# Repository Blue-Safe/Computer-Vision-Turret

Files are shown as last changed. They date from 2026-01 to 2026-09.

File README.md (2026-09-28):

# Computer Vision Turret (CVT)

CVT is a real-time computer vision turret designed to track a moving black target from ~5 ft away and maintain alignment within one-fourth of the target’s area.  
The system combines proportional and predictive control and is split across a Raspberry Pi 5 (vision and logic) and a Raspberry Pi Pico (servo and laser control).

> This project was designed, built, tested, and documented independently.

## Skills Demonstrated

- Embedded systems architecture with delegated responsibility
- Computer vision with OpenCV
- Real time control concepts
- UART communication
- Data logging and statistical analysis
- Test design and performance evaluation
- Iterative debugging across software and hardware

### Mechanical Design

- Custom turret frame modeled in Fusion 360
- 3D printed structural and mounting componets
- Design iteration focused on rigidity, airflow, and quick iterations 

## System Architecture

### Raspberry Pi 5 (High-Level Control)
- Captures live video feed from webcam
- Performs computer vision using OpenCV
- Determines system state and target behavior
- Estimates target velocity and predicts future position
- Sends motion commands to the Pico over UART

### Raspberry Pi Pico (Real-Time Control)
- Receives commands from the Pi
- Converts desired angles into PWM signals
- Drives X/Y servos and toggles the laser

## Videos and Pictures

**Demo**  
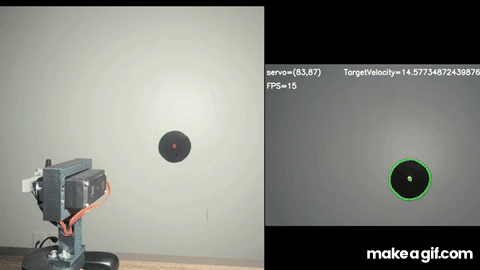
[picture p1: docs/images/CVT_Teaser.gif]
CVT Teaser


**Full Test Footage**
- Static target test: [Here](https://youtu.be/bPHvd_qhFpg)
- Dynamic target test: [Here](https://youtu.be/34uFZd7rjXk)

### Build Photos

| Front | Side |
|---|---|
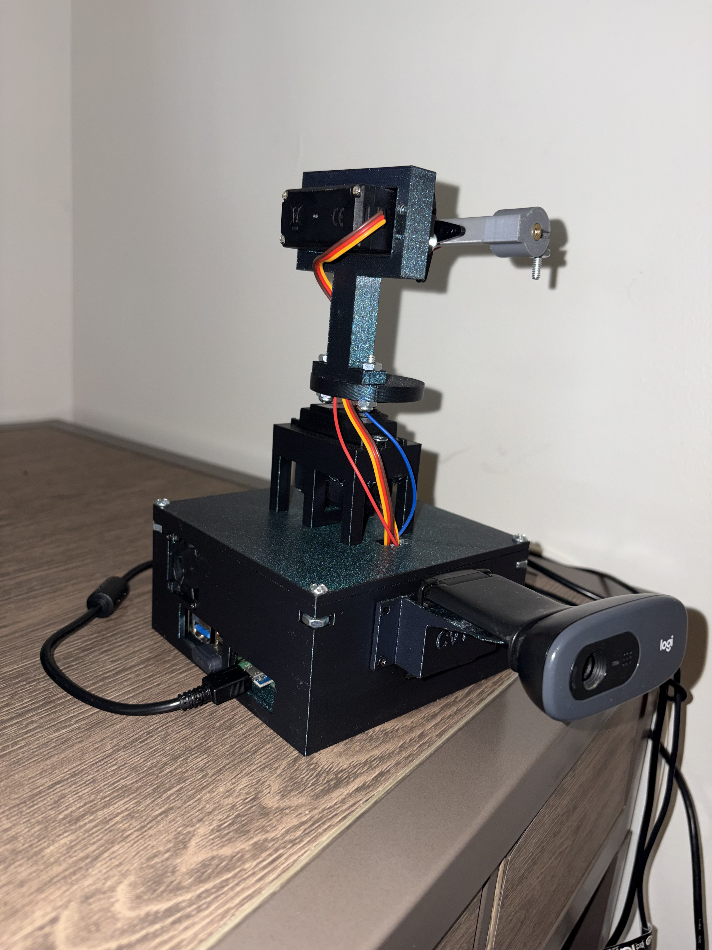
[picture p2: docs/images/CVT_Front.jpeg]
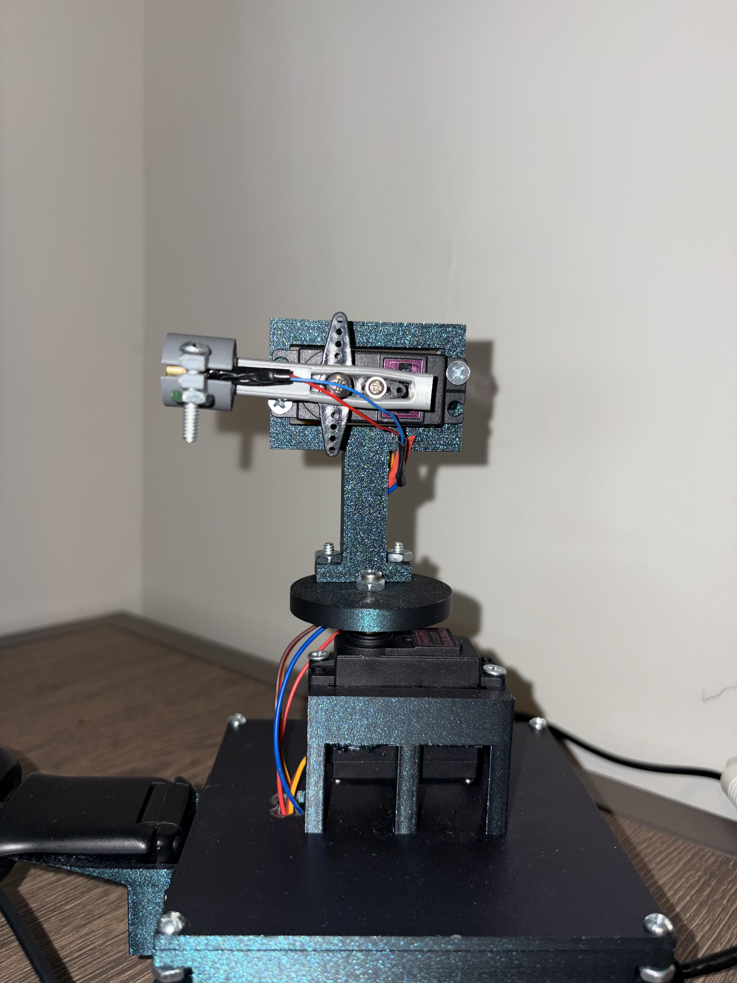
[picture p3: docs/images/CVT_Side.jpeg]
|  |  |

| Inside | Rear |
|---|---|
|  |  |

## What It Does

- Detects a target in a live camera feed 
- Determines target position and laser position, then calculates pixel error
- Stores information of target and the turrets current state
- Applies proportional and predictive movement, deadbanding, and motion constraints
- Converts pixel error into servo motion commands
- Maintains tracking under target motion and noise
- Logs runtime data to CSV for performance analysis

## Control Loop Overview

1. Capture frame  
2. Threshold and filter to isolate target then laser  
3. Extract contours and select best candidate based on expected area and color  
4. Compute target center and pixel error  
5. Apply control logic (proportional and predictive)  
6. Send servo commands over UART  
7. Log timestamped data (position, error, velocity, state)

## Results and Performance

### Tracking Error vs Target Velocity
This plot compares tracking error against target velocity over time, highlighting the velocity range where the system performs reliably and where hardware limits (camera FPS) introduce error. You can see tracking error increase once target velocity exceeds ~125 px/s, which correlates with the system's frame rate and control update limits.

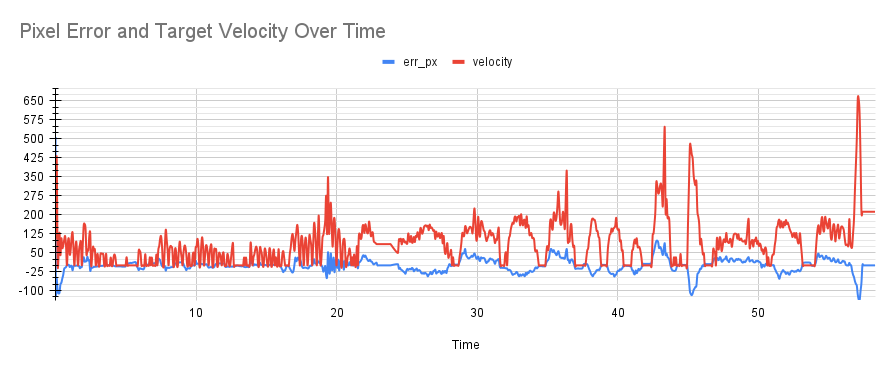
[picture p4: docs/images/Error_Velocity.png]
Error vs Velocity


### Lock-In Time Histogram
Distribution of Lock-In times. Locked In was defined as remaining within one-fourth the area of the target for half a second. CVT averaged a lock in time of .98 seconds, with a standard deviation of .27 seconds. By the Lock-In definition, acquisition time is around .48 seconds.

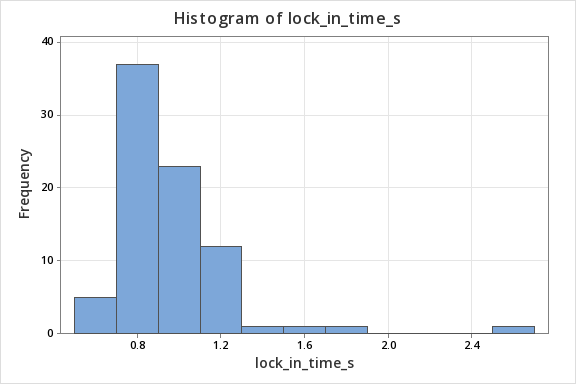
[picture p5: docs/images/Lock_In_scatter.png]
Lock-In Histogram


### Limitations and Constraints

- Camera operates at ~15 FPS, limiting control update rate
- Higher target velocities (>125 px/s) increase tracking error
- Lighting conditions affect thresholding reliability

These constraints were intentionally measured and documented to define realistic system performance bounds. See [this log](data/sample/DYNAMIC_TARGET.csv) for documented framerate.

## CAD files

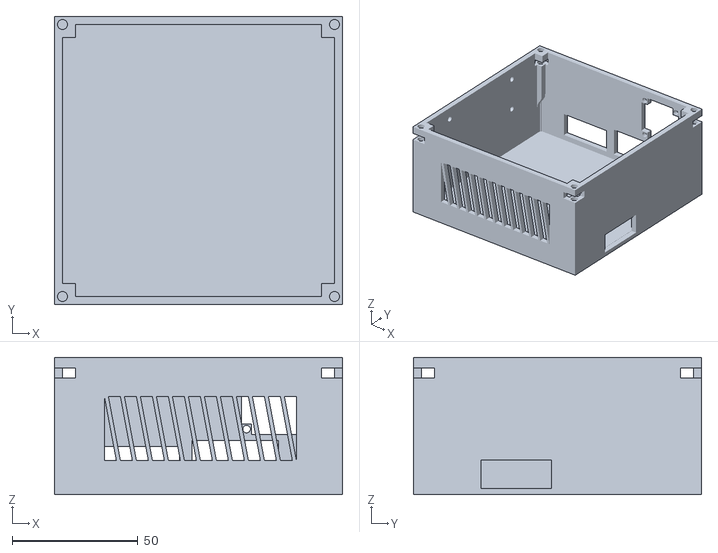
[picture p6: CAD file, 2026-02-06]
stl/CVT_Base.stl
114.3 x 114.3 x 54.5

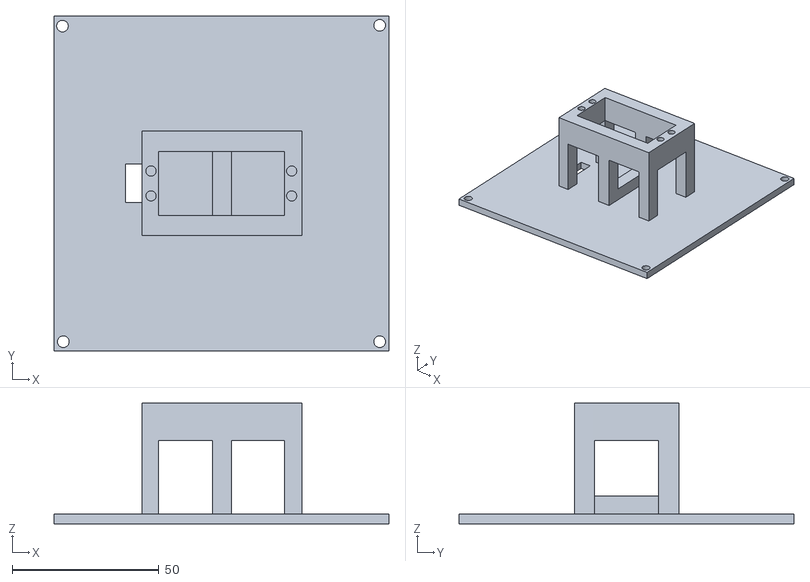
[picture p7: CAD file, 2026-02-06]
stl/CVT_Lid.stl
114.3 x 114.3 x 41.2

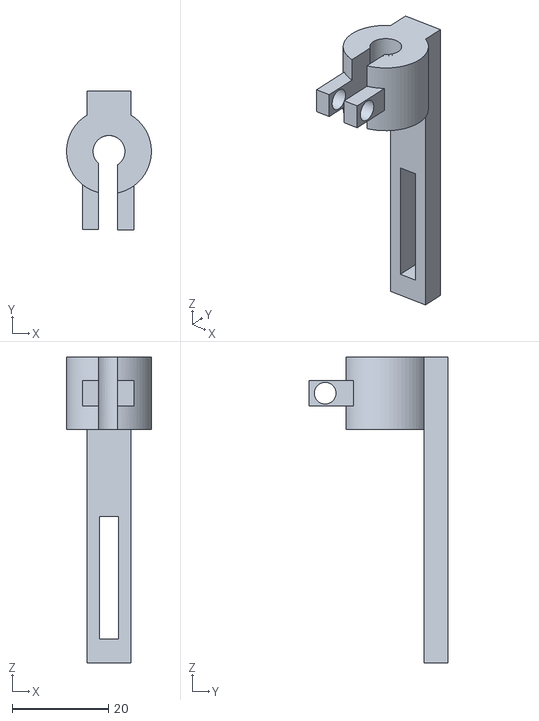
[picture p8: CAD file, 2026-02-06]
stl/CVT_LaserMount.stl
17.6 x 28.8 x 63.5

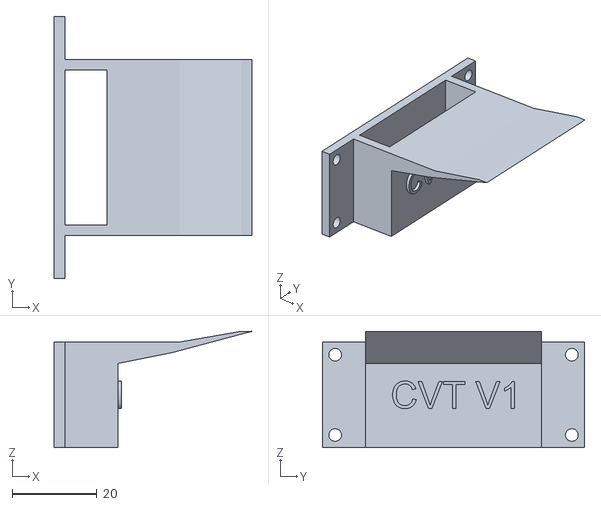
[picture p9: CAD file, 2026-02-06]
stl/CVT_CameraMount.stl
46.8 x 62.0 x 27.5

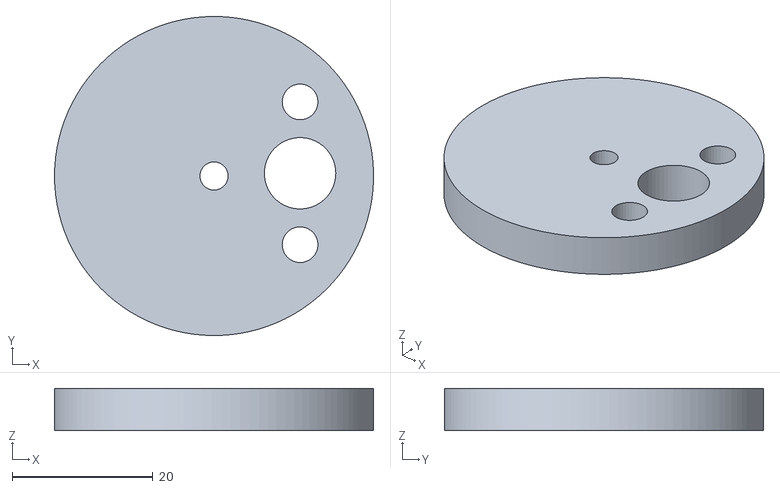
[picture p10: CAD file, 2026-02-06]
stl/CVT_AxisAdapter.stl
45.4 x 45.4 x 6.00

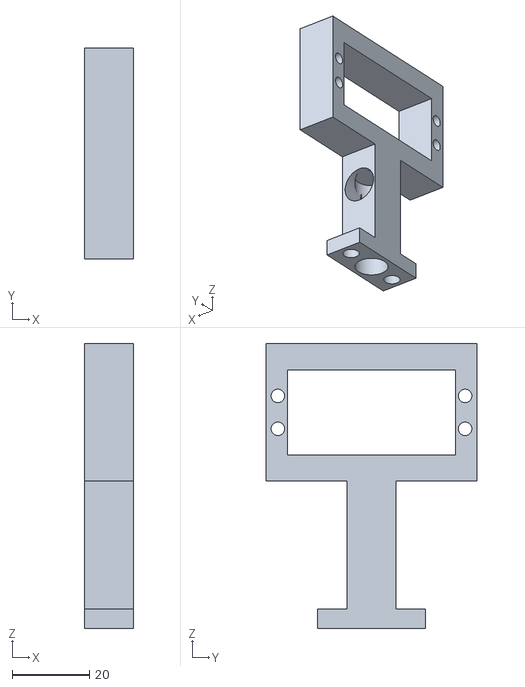
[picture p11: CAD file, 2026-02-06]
stl/CVT_ServoMount.stl
12.7 x 54.6 x 73.7

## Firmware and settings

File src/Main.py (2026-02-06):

import cv2
import numpy as np
import time
import math
import csv
from pathlib import Path
from enum import Enum, auto
from dataclasses import dataclass
from Servo_Control import sendData

# Tunable Variables 
DEADBAND_PX = 7
LASER_AREA  = 5000
TARGET_AREA = 8000
LOCKED_PX = math.sqrt(TARGET_AREA / math.pi) / 2
MAX_ANGLE = 170
MIN_ANGLE = 10
MAX_ANGLE_JUMP = 30
LOST_COUNT = 15
PTD_CONSTANT = 0
VEL_THRESHOLD = 30
T_LEAD = .22
LOCKED_TIME =.5
CONFIDENCE_THRESHOLD = 80
TAU = 0.7
WIDTH = 640
HEIGHT = 480
DIVISIONS = 10

# Invert if turret tracks in the wrong direction
INVERT_X = True
INVERT_Y = False

# Turn on/off debugging tools
Debug = False
UI = True
frameRate = True
AllMasks = False

# Establish States

class State(Enum):
    TRACK = auto()
    IDLE = auto()
    INIT = auto()
    TESTONE = auto()
    TESTTWO = auto()


# Define Turret object. This organizes the variables I edit in many
# spots, without having the headache of globals

@dataclass
class Turret:
    state: State = State.INIT
    servo_x: float = 90.0
    servo_y: float = 90.0
    home_pos: tuple[int,int] = (0,0)
    target_pos: tuple[int,int] = (0,0)
    last_target: tuple[int,int] = (0,0)
    laser_pos: tuple[int,int] = (0,0)

    lost_counter: int = 0
    locked: bool = False
    lock_start: float = 0.0
    lock_in_time: float = 0.0
    t_lock: float = 0.0
    confidence: float = 0.0
    accuracy: float = 0.0

class CSVLogger:

    def __init__(self):
        self.f = None
        self.w = None
        self.t0 = None

    def start(self, filename: str):
        Path("logs").mkdir(exist_ok=True)
        self.f = open(Path("logs") / filename, "w", newline="")
        self.w = csv.writer(self.f)
        self.t0 = time.perf_counter()

        self.w.writerow([
            "t", "dt", "fps", "state",
            "laser_x", "laser_y",
            "target_x", "target_y",
            "dx", "dy", "err_px",
            "vx", "vy", "velocity",
            "servo_x", "servo_y",
            "locked", "t_lock",
            "lost_counter"
        ])



    def log_frame(self, t: Turret, dt, dx, dy, err_px, vx=0,vy=0):
        if self.w is None:
            return

        rel_t = time.perf_counter() - self.t0

        self.w.writerow([
            round(rel_t, 4), round(dt, 4), round(1.0/dt), t.state.name,
            int(t.laser_pos[0]), round(1.0/dt), int(t.laser_pos[1]),
            int(t.target_pos[0]), int(t.target_pos[1]),
            round(dx, 3), round(dy, 3),
            round(vx,3), round(vy,3),round(math.hypot(vx+.00001,vy+.00001)),
            round(err_px, 3),round(t.servo_x, 3), round(t.servo_y, 3),
            int(t.locked), round(t.t_lock, 4)
        ])

    def stop(self):
        if self.f:
            self.f.close()
        self.f = None
        self.w = None
        self.t0 = None

    @property
    def enabled(self):
        return self.w is not None

class Dummytarget:

    pos: tuple[int,int] = (0,0)
    velocity: tuple[float,float] = (0.0,0.0)
    area: float = TARGET_AREA 

    def __init__(self,pos,velocity):
        self.pos = pos
        self.velocity = velocity

    def move(self,dt):
        # Determine next position based off of the current velocity and time passed.

        x,y = self.pos
        dx,dy = self.velocity[0]*dt,self.velocity[1]*dt
        self.pos = x+dx,y+dy

def save_trials_csv(time_trials: dict, filename: str):
    Path("logs").mkdir(exist_ok=True)
    with open(Path("logs")/filename, "w", newline="") as f:
        w = csv.writer(f)
        w.writerow(["trial_id","goal_x","goal_y","lock_in_time_s"])
        for i, ((x,y), tlock) in enumerate(time_trials.items()):
            w.writerow([i, x, y, tlock])


def largest_center_from_mask(mask, min_area,max_area):
    # Helper function that finds all contours within the frame, then orgainzes them
    # and returns the position and contour object that is the largest within the range 
    # Passed through the parameters

    contours, _ = cv2.findContours(mask, cv2.RETR_EXTERNAL, cv2.CHAIN_APPROX_SIMPLE)
    valid = []
    for c in contours:
        if cv2.contourArea(c) >= min_area and cv2.contourArea(c) <= max_area:
            valid.append(c)
    
    if not valid:
        return None, None
    
    c = max(valid, key=cv2.contourArea)
    x, y, w, h = cv2.boundingRect(c)
    cx, cy = x + w // 2, y + h // 2
    if Debug:
        print(f"Biggest Blob size: {cv2.contourArea(c)}")
    return (cx, cy), c

def detect_laser(frame_bgr):
    hsv = cv2.cvtColor(frame_bgr, cv2.COLOR_BGR2HSV)

    # Laser appears bright red and white hot to the webcam. I use three ranges, as red wraps around the scale and
    # If we don't account for the white center, it'll be a donut shape rather than our whole laser.
    RL1, RU1 = (0, 60, 120), (10, 255, 255)
    RL2, RU2 = (170, 60, 120), (179, 255, 255)
    WL, WU = (0, 0, 200), (179, 10, 255)

    m1 = cv2.inRange(hsv, RL1, RU1)
    m2 = cv2.inRange(hsv, RL2, RU2)
    m3 = cv2.inRange(hsv, WL, WU)


    # To get each pixal we picked out, we have to or all our maskes together. We have to embedded the call
    # Inside because it only takes two arguments
    mask = cv2.bitwise_or(cv2.bitwise_or(m1, m2), m3)

    # Help clean specks
    mask = cv2.medianBlur(mask, 5)

    # Pass off to our helper to get the largest blobs center.
    # Range is geneours because the webcame is noisy.
    center, contour = largest_center_from_mask(mask, LASER_AREA-5000,LASER_AREA+5000)

    # Return the center cord, the masked frame incase we want to display it, and the actual object itself. 
    return center, mask, contour

def detect_target(frame_bgr, laser_mask=None):

    # The goal of this helper is to find the largest object in the frame while not picking up the laser.
    # Thats why we pass laser_maks through, so we automatically block out where it is from the target mask.
    
    # Convert color range to hsv for color tracking

    hsv = cv2.cvtColor(frame_bgr, cv2.COLOR_BGR2HSV)

    # Filter for colors within the expected color range of the target.

    BL,BU = (0,0,0),(179,255,50)


    mask = cv2.inRange(hsv,BL,BU)

    

    # This is where we block out where the laser is in the frame, or atleast where it was when we last located it.
    if laser_mask is not None:
        inv_laser = cv2.bitwise_not(laser_mask)
        mask = cv2.bitwise_and(mask, inv_laser)

    # Pass off largest blob detection to helper function.

    center, contour = largest_center_from_mask(mask, TARGET_AREA-3000, TARGET_AREA+3000)
    
    return center, mask, contour

def clamp(val, low, high):
    return max(low, min(high, val))

def move_servos(t:Turret,dx,dy,gain):
    # Moves the servos based on their current position, the error, and gain.

    # If Servo moves in the wrong direction flip axis's
    if INVERT_X:
        dx = -dx
    if INVERT_Y:
        dy = -dy

    # pixels to degrees
    X_degree = (dx / PTD_CONSTANT) * gain
    Y_degree = (dy / PTD_CONSTANT) * gain

    # Clamp angle change and new servo position
    X_degree = clamp(X_degree, -MAX_ANGLE_JUMP, MAX_ANGLE_JUMP)
    Y_degree = clamp(Y_degree, -MAX_ANGLE_JUMP, MAX_ANGLE_JUMP)

    t.servo_x = clamp(t.servo_x + X_degree, 0, 180)
    t.servo_y = clamp(t.servo_y + Y_degree, 0, 180)

    sendData(t.servo_x, t.servo_y, 1)

def demo_track(test):

    # Initializing code. Starts up required variables and locates laser home position.

    global PTD_CONSTANT
    global MAX_ANGLE_JUMP
    turret = Turret()
    logger = CSVLogger()
    
    # Grab webcam data, define resolution, and only let 1 frame sit in buffer
    cap = cv2.VideoCapture(0)
    cap.set(cv2.CAP_PROP_FRAME_WIDTH, 640)
    cap.set(cv2.CAP_PROP_FRAME_HEIGHT, 480)
    cap.set(cv2.CAP_PROP_BUFFERSIZE, 1)

    if not cap.isOpened():
        print("Could not open Camera")
        return

    lastfps = 0
    prev_t = time.perf_counter()
    
    while True:
        
        target_contour = None
        laser_contour = None
        target_mask = None
        laser_mask = None
        target_center = None
        laser_center = None
        ret = False
        frame = None

        now = time.perf_counter()
        dt = now - prev_t
        prev_t = now

        # Due to my lower framerate,if there is a significant stutter dt would become larger
        # Then what we would want it to be. Clamp to a reasoble time
        dt = clamp(dt,.01,.1) 
        
        if turret.state is not State.INIT:

            # Read in new frame each loop

            cap.grab()
            ret, frame = cap.retrieve()

            if not ret:
                break

            # Detect Laser and Target.

            laser_center, laser_mask, laser_contour = detect_laser(frame)
            target_center, target_mask, target_contour = detect_target(frame, laser_mask=laser_mask)
            
            # Store current data. If no laser or target is picked up, assume last position.
             

            if laser_center != None:
                turret.laser_pos = laser_center

            if target_center != None:
                turret.target_pos = target_center

            # Calculate error

            if laser_center != None and target_center != None:
                dx = target_center[0] - laser_center[0]
                dy = target_center[1] - laser_center[1]
            else:
                dx,dy = 0,0

            err_px = math.hypot(dx, dy)
            
                
        if turret.state is State.INIT:
            # In the setup state, we find the PTD_CONSTANT,

           
            sendData(80,90,1)
            time.sleep(.5)

            ret, frame = cap.read()
            laser_center,laser_mask, laser_contour = detect_laser(frame)
            leftPos = laser_center

            sendData(90,90, 1)
            time.sleep(.5)

            ret, frame = cap.read()
            laser_center,laser_mask, laser_contour = detect_laser(frame)
            homePos = laser_center
            turret.home_pos = homePos

            sendData(100,90,1)
            time.sleep(.5)

            ret, frame = cap.read()
            laser_center,laser_mask, laser_contour = detect_laser(frame)
            RightPos = laser_center
          
            L_pixel_delta = leftPos[0] - homePos[0]
            R_pixel_delta = RightPos[0] - homePos[0]

            PTD_CONSTANT = ((abs(L_pixel_delta) + abs(R_pixel_delta)) / 2) / 10

            if Debug:
                print(f"PTD_CONSTANT: {PTD_CONSTANT}")

            
            sendData(90,90,1)
            time.sleep(.5)
            
            # Switch states
            turret.state = State.IDLE
            MAX_ANGLE_JUMP = 3
            gain = .1
        
        elif turret.state is State.IDLE:
            # In the Idle state, we first check if we see a target or not. 
            # If we don't, we track the home position slowly, in case the target comes back on frame.
            # Then we ensure we do a check to ensure we are still within the expected range.

            gain = .1
            
            if target_contour is not None:
                turret.state = State.TRACK
                turret.lost_counter = 0
                MAX_ANGLE_JUMP = 13
                turret.last_target = target_center
                turret.locked = False
                turret.t_lock = 0.0
                turret.confidence = 0.0
                turret.accuracy = 0.0
                turret.lock_in_time = 0.0
                turret.lock_start = time.perf_counter()
            else:
                turret.target_pos = turret.home_pos
                dx = turret.target_pos[0] - turret.laser_pos[0]
                dy = turret.target_pos[1] - turret.laser_pos[1]

                move_servos(turret,dx,dy,gain)

                if turret.servo_x > MAX_ANGLE or turret.servo_x < MIN_ANGLE or turret.servo_y > MAX_ANGLE or turret.servo_y < MIN_ANGLE:
                    sendData(90,90,1)
                    turret.servo_x, turret.servo_y = 90,90
                    time.sleep(.4)
        
        elif turret.state is State.TESTTWO:
            # In the tracking state,

            gain = .25

            if target_contour is not None:
                
                # when we see the target, start decreasing the counter till we hit zero.
                turret.lost_counter = max(0,turret.lost_counter-1)

                # Get targets Velocity
                last_target = turret.last_target
                vx = (target_center[0] - last_target[0]) / dt
                vy = (target_center[1] - last_target[1]) / dt
                
                if abs(vx) < VEL_THRESHOLD:
                    vx = 0
                if abs(vy) < VEL_THRESHOLD:
                    vy = 0

                ptx = target_center[0] + vx * T_LEAD
                pty = target_center[1] + vy * T_LEAD
                
                # calculate error from laser to target. Add .001 so it is unlikely to be zero
                dx = ptx - turret.laser_pos[0]+.001 
                dy = pty - turret.laser_pos[1]+.001
                
                err = math.hypot(dx, dy)

                # Accuracy score 0-1
                turret.accuracy = clamp(1.0 - (err / LOCKED_PX), 0.0, 1.0)

                # Time-on-target score 0-1
                if err < LOCKED_PX:
                    turret.t_lock += dt
                else:
                    turret.t_lock = 0.0

                if turret.t_lock >= LOCKED_TIME and not turret.locked and turret.confidence >= CONFIDENCE_THRESHOLD:
                    lock_end = time.perf_counter()
                    turret.locked = True
                    turret.lock_in_time = lock_end-turret.lock_start
                time_confidence = 1.0 - math.exp(-turret.t_lock / TAU)

                turret.confidence = 100.0 * turret.accuracy * time_confidence
                
                if err > DEADBAND_PX:
                    
                    move_servos(turret,dx,dy,gain)

            else:
                turret.lost_counter += 1
                if turret.lost_counter >= LOST_COUNT:
                    turret.state = State.IDLE
                    turret.accuracy = 0.0
                    turret.t_lock = 0.0
                    time_confidence = 0.0
                    turret.confidence = 0.0

            if turret.servo_x > MAX_ANGLE or turret.servo_x < MIN_ANGLE or turret.servo_y > MAX_ANGLE or turret.servo_y < MIN_ANGLE:
                print("LIMIT RESET TRIGGERED")
                sendData(90,90,1)
                turret.servo_x, turret.servo_y = 90,90
                time.sleep(.4)
             
        if UI and frame is not None:

            vis = frame.copy()

            # Draw detections onto the frame for debugging
            if laser_contour is not None:
                cv2.drawContours(vis, [laser_contour], -1, (0, 255, 255), 2)
            if target_contour is not None:
                cv2.drawContours(vis, [target_contour], -1, (0, 255, 0), 2)

            # UI
            cv2.circle(vis, (turret.laser_pos), 5, (0, 255, 255), -1)
            cv2.circle(vis, (turret.target_pos), 5, (0, 255, 0), -1)
            cv2.line(vis, (turret.laser_pos), (turret.target_pos), (255, 255, 255), 1)
            cv2.putText(vis, f"servo=({round(turret.servo_x)},{round(turret.servo_y)})    State={turret.state}   "     ,(10, 30), cv2.FONT_HERSHEY_SIMPLEX, 0.7, (255,255,255), 2)
            cv2.putText(vis, f"FPS={round(lastfps)}    Confidence={round(turret.confidence,2)} Lock in time={round(turret.lock_in_time,2)}"     ,(10, 70), cv2.FONT_HERSHEY_SIMPLEX, 0.7, (255,255,255), 2)
            if not ret or vis is None or vis.size == 0:
                continue
            else:
                cv2.imshow("Webcam", vis)


                if AllMasks:
                    if target_mask is not None and target_mask.size > 0 and laser_mask is not None and laser_mask.size > 0:
                        cv2.imshow("target_mask", target_mask)
                        cv2.imshow("laser_mask", laser_mask)

            
        lastfps = 1.0 / dt
        if target_center is not None:
            turret.last_target = target_center

        key = cv2.waitKey(1) & 0xFF

        if key == ord('q'):
            break

        if key == ord('l') and not logger.enabled:
            logger.start(f"run_{int(time.perf_counter())}.csv")
            print("LOGGING ON")

        if key == ord('k') and logger.enabled:
            logger.stop()
            print("LOGGING OFF")

    cap.release()
    logger.stop()
    cv2.destroyAllWindows()
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

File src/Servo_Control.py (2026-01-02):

import time
import math
import serial

ser = serial.Serial("/dev/ttyAMA0", 115200, timeout=0)


def sendData(x,y,laser=0):
    x = max(0, min(180,int(x)))
    y = max(0, min(180,int(y)))
    ser.write(bytes([0xFF,x,y,laser]))



def drawCircle(center, radius_deg, step_deg, delay):
    
    cx, cy = center
    for theta in range(0, 360, step_deg):
        
            
            
            rad = math.radians(theta)
            x = cx + radius_deg * math.cos(rad)
            y = cy + radius_deg * math.sin(rad)

            # clamp to safe servo range

            x = max(0, min(180, x))
            y = max(0, min(180, y))

            sendData(x,y,1)
            time.sleep(delay)

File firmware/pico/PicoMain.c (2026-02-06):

#include <stdint.h>
#include <stdbool.h>
#include "pico/stdlib.h"
#include "hardware/pwm.h"
#include "hardware/uart.h"

#define LASER_PIN 16
#define LED_PIN 25
#define BAUDRATE 115200


#define SERVO_X_PIN 14
#define SERVO_Y_PIN 15
#define SERVO_MIN_US 1000
#define SERVO_MAX_US 2000
#define SERVO_PERIOD 20000

uint16_t angle_to_us(uint8_t angle) {
    return SERVO_MIN_US + ( (SERVO_MAX_US - SERVO_MIN_US) * angle) / 180;
}

void set_servo_angle(uint gpio_pin, uint8_t angle) {
    uint slice = pwm_gpio_to_slice_num(gpio_pin);
    uint chan  = pwm_gpio_to_channel(gpio_pin);

    uint16_t us = angle_to_us(angle);
    pwm_set_chan_level(slice, chan, us);
}



int main() {

    /* Set up LED_PIN & LASER_PIN*/

    gpio_init(LED_PIN);
    gpio_set_dir(LED_PIN,true);

    gpio_init(LASER_PIN);
    gpio_set_dir(LASER_PIN,true);

    /* Set up PWM control*/

    gpio_set_function(SERVO_X_PIN, GPIO_FUNC_PWM);
    gpio_set_function(SERVO_Y_PIN, GPIO_FUNC_PWM);

    uint slicex = pwm_gpio_to_slice_num(SERVO_X_PIN);
    uint slicey = pwm_gpio_to_slice_num(SERVO_Y_PIN);

    pwm_config cfg = pwm_get_default_config();
    pwm_config_set_clkdiv(&cfg,125);
    pwm_config_set_wrap(&cfg, SERVO_PERIOD - 1);

    pwm_init(slicex, &cfg,true);
    pwm_set_enabled(slicex,true);
    pwm_init(slicey, &cfg,true);
    pwm_set_enabled(slicey,true);


    /* Set up UART communication*/

    uart_init(uart0, 115200);
    gpio_set_function(0, GPIO_FUNC_UART); // TX
    gpio_set_function(1,GPIO_FUNC_UART); // RX
    uart_set_format(uart0, 8, 1, UART_PARITY_NONE);

    enum {WAIT, READ_X, READ_Y,LASER} state = WAIT;

    uint8_t x = 90;
    uint8_t y = 90;
    bool laser = false;

    set_servo_angle(SERVO_X_PIN,x);
    set_servo_angle(SERVO_Y_PIN,y);
    gpio_put(LASER_PIN,false);

    while (true) {
        if (uart_is_readable(uart0)) {
            uint8_t b = uart_getc(uart0);
            gpio_put(LED_PIN, true);
            
            switch (state) {
                case WAIT:
                    if (b == 0xFF) {
                        state = READ_X;
                    }
                    break;
                case READ_X:
                    x = b;
                    state = READ_Y;
                    break;
                case READ_Y:
                    y = b;
                    state = LASER;
                    set_servo_angle(SERVO_X_PIN,x);
                    set_servo_angle(SERVO_Y_PIN,y);
                    break;
                case LASER:
                    state = WAIT;
                    if (b == 0x01) {
                        laser = true;
                    } else {
                        laser = false;
                    }
                    gpio_put(LASER_PIN,laser);
                    break;
                default: 
                    state = WAIT;
                    break;
            }
        }
    }

}

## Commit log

2025-12-06 Got Tracking working, and wrote test script for servo calibration
2025-12-06 Changed Servo Control to my PCA board
2025-12-09 Developing Calibration
2025-12-09 Developing the calibration method
2026-01-01 Changed Laser and Servo control to PICO rather than the PCA board. Updated ServoTesting.py. Replaced SetPos() with sendData().
    [Main.py]
2026-01-06 Archiving Current version before revamping for state machine
2026-01-15 Second Draft of state machine. Also added confidence tracking and timer for lock in time.
2026-02-04 Completed Testing
    [DYNAMIC_TARGET.csv, STATIC_TARGET_LOG.csv, STATIC_TARGET_TIMES.csv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]
2026-02-06 Organized Repo
    [DYNAMIC_TARGET.csv, STATIC_TARGET_LOG.csv, STATIC_TARGET_TIMES.csv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]
2026-02-06 Added STL files
    [CVT_AxisAdapter.stl, CVT_Base.stl, CVT_CameraMount.stl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]
